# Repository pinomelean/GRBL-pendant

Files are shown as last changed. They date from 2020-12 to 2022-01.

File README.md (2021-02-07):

# GRBL-pendant

Hardware pendant intended for use with G-code senders for GRBL machines

### Description
The aim of this project is to produce a physical controller which functions similarly to a machine pendant, but is not limited to only that. The device would allow the user to interact with both the computer and the CNC machine without needing to reach for the mouse and keyboard for the most machining tasks.
The hardware is not limited to a single purpose, though, as the firmware can be easily changed so the controller can suit the needs of the user, and be adapted for their particular workflow.

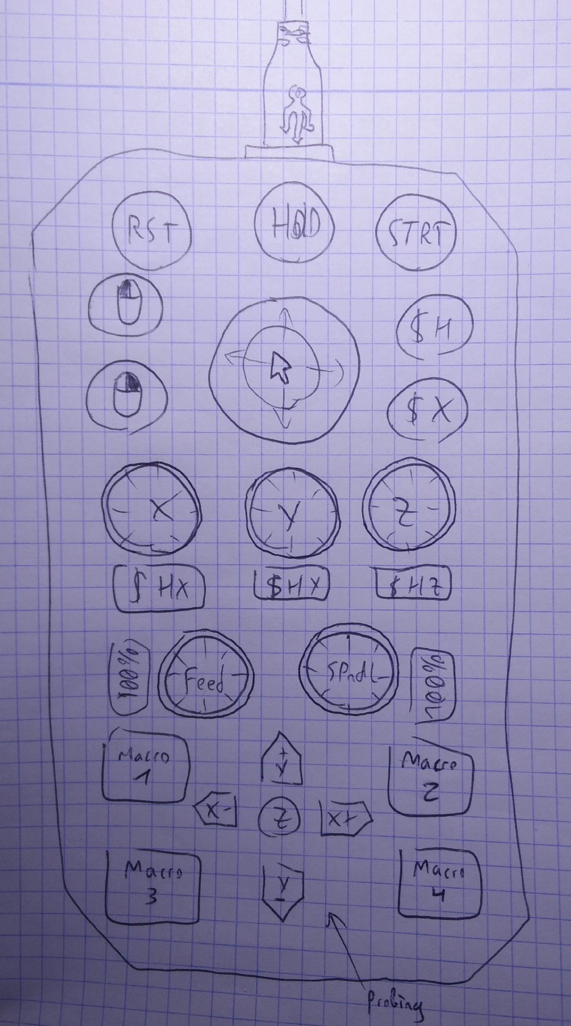
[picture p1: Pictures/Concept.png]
Initial concept drawing
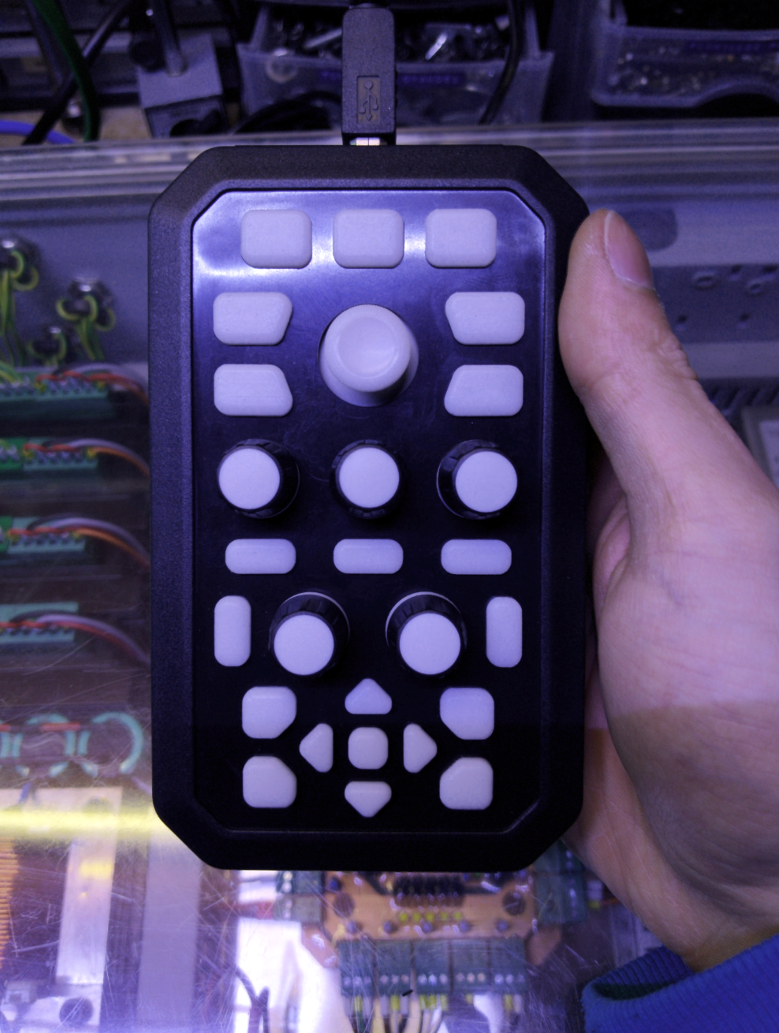
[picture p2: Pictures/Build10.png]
 	  

This USB pendant Includes many buttons, encoders and a thumbstick that can be configured with the most common functions and G-code commands you need to use your machine.
It uses a Teensy++ 2 because of its physical size, IO, native USB, and ease of programming with the Arduino ecosystem, *as limited as it is*.

### Free and open source

I publish all the files necessary for anyone to "DIY" it, all files can be opened and edited with FOSS software.
Anyone with a CNC mill/router should be able to make their own if they're so inclined.

The code is written as simple as I can manage (even if I suck at it), so anyone with basic knowledge and/or an Arduino tutorial open in another tab can modify it to suit their needs.

The PCBs are designed in KiCad and made to be simple enough to be milled at home, as I've done with the first prototype.

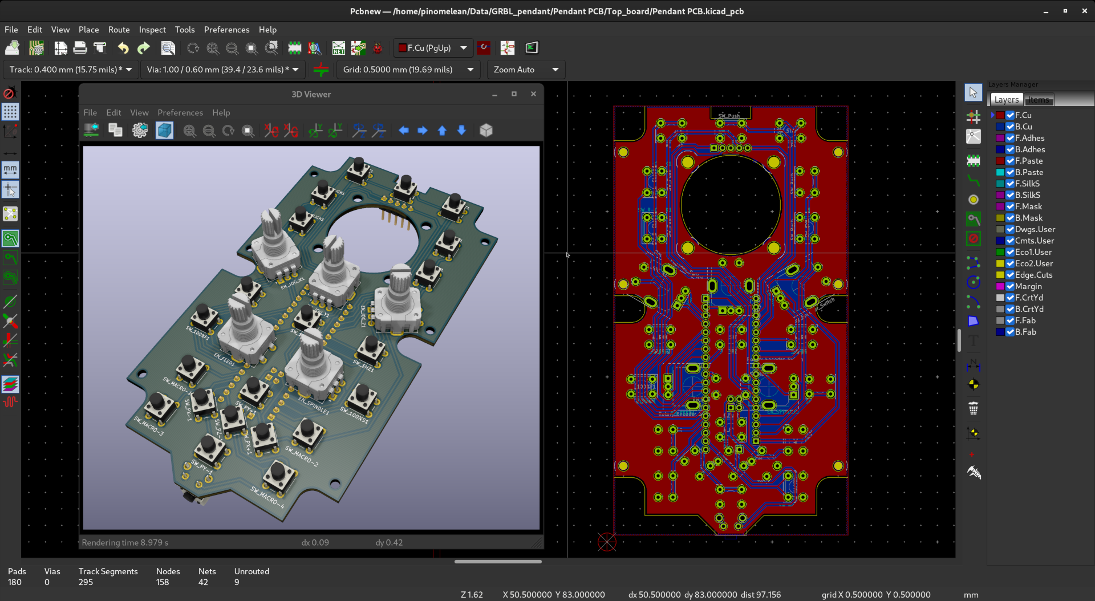
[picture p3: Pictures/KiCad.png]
KiCad


To mill the PCBs I used, and would recommend, [Juan Pablo Caram](https://github.com/jpcaram)'s [FlatCAM](http://www.flatcam.org/) and [Martin Pittermann](https://github.com/martin2250)'s [OpenCNCPilot](https://github.com/martin2250/OpenCNCPilot)

FreeCAD was used to design the silicone keypad and the mould to cast it.
The mould and the case were milled using toolpaths generated in the path workbench.

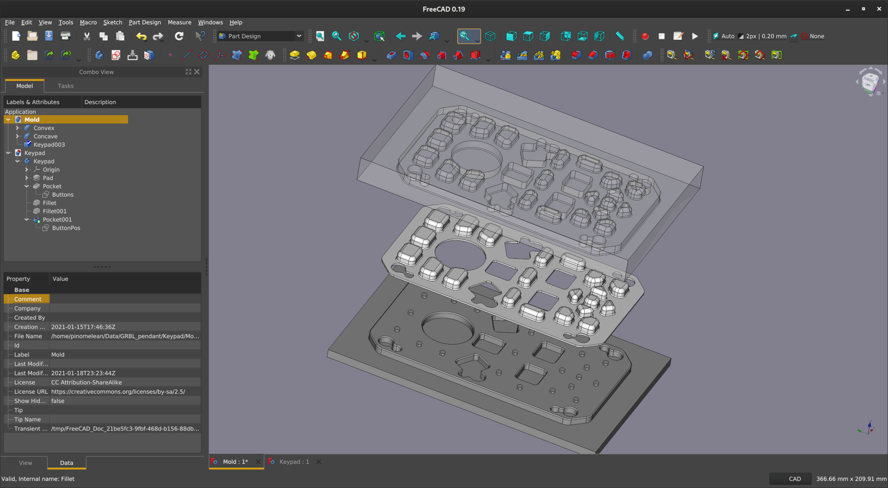
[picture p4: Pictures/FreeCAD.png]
FreeCAD


## Pendant layout

The layout I had in mind designing this pendant, and will come by default will be the following:

The Thumbstick is used either as a mouse pointer, along with a couple of buttons for clicking, or to quickly jog the machine when pressed in.

*The Teensy can emulate a game controller thumbstick, but as not many G-code sender applications support game controllers, and those that do (I only tested UGS) may not recognize the one emulated by the teensy, the thumbstick will not be emulating a game controller for nw, and just write G-code jog commands instead. This should work with any sender.*

The buttons at the top of the pendant are dedicated to the basic machine commands: Reset, Feed hold, Cycle start/Resume at the top, and Home machine and Kill alarm lock right of the thumbstick.

There are three encoders for fine jogging of each axis. By default each detent should result in 1mm of travel, and 0.1mm if the encoder is pushed in while turning.
Pushing an encoder without turning it will zero that axis.

The two other encoders are meant for Feed and spindle speed overrides, but could be used for jogging two extra axises in a 5-axis machine if anyone's running one of those.

*I still need to figure how to send the Feed and Spindle speed override command characters through a sender application if it does not have hotkeys for that*

Next to each encoder is a button which is used to individually home that axis.
For the Feed and Spindle encoders, the button resets it to 100%.

At the bottom of the controller are the macro buttons.
The five ones in the middle are used for probing or touching against a workpiece from every direction (except from under it).

The other 4 buttons are left for any extra macros the user could need, such as turning on/off mist/flood coolant, starting/stopping the spindle, touching a bit on the tool setter...

**Of course, all of the actions are remappable and configurable to suit the needs and workflow of the user. The defaults are just what** ***I*** **think is most useful**

## Project status

- Second version built. Looks much nicer in black and white. Probably final version if no issues arise.
	- The keypad also feels nice and works very well, but the Shore A20 durometer silicone might be too soft for this application, but will do for mow.



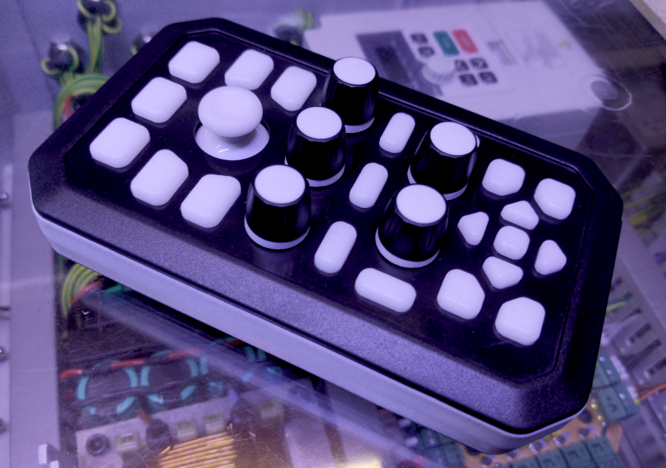
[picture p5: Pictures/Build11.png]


- Keypad mould machined. Couldn't get the 3D surfacing operation to work with a ball end mill en FreeCAD, so I had to resort to Fusion360 for that operation.
	- A sprue and vent have to be drilled manually into the side to inject the silicone with a syringe and push out the air.

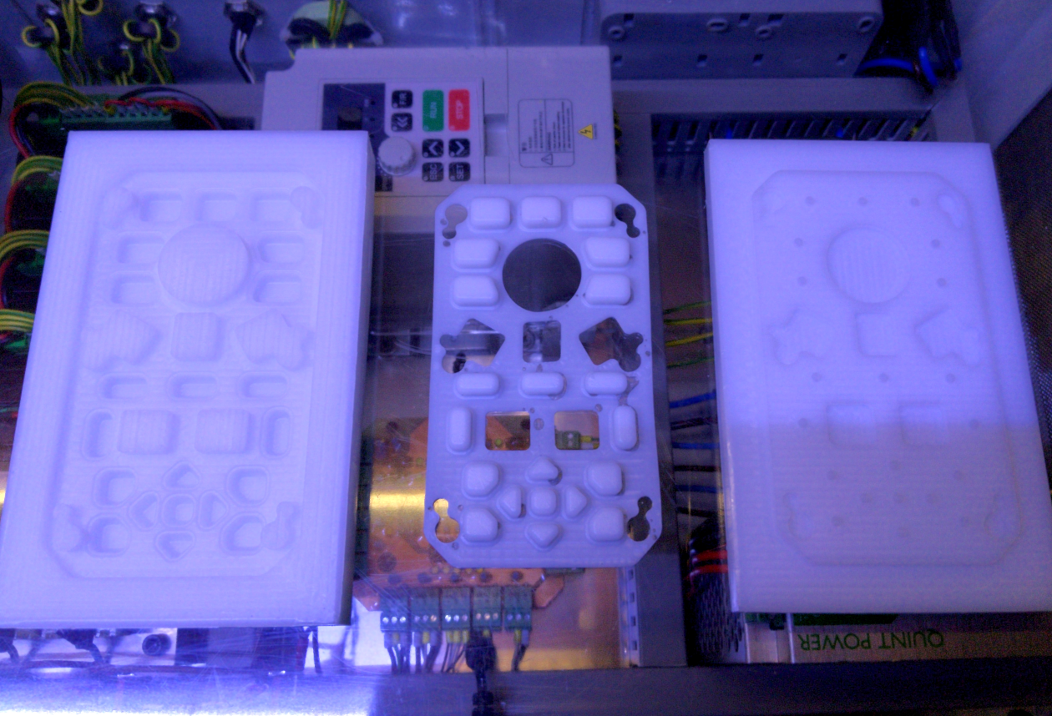
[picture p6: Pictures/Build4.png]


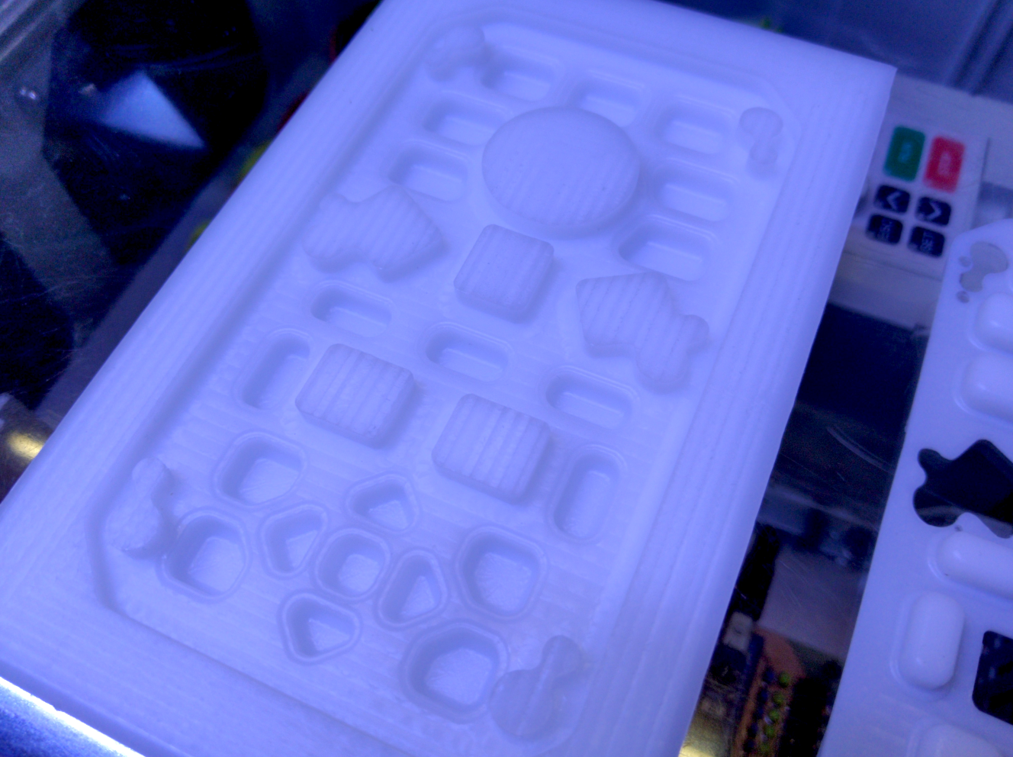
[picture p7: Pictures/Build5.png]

	
- First prototype mostly built, silicone keypad left to see how it all looks and feels. A couple of encoder push buttons don't work, but will do for testing.
	- Several adjustments made for a second version. Will not make a mold and keypad for the first.



- Thumbstick as mouse pointer - Done. Works pretty well in the smaller screens I use, slower in bigger ones, but it's adjustable.
- Thumbstick for jogging - UGS wouldn't recognize it in game controller mode, so It just types jogging G-code commands. Works ok.
- Encoder jogging - Works well for accurate positioning. Too slow for jogging around a bigger machine, but there's the thumbstick for that.
- Rest of the buttons - not yet programmed.

## Notes

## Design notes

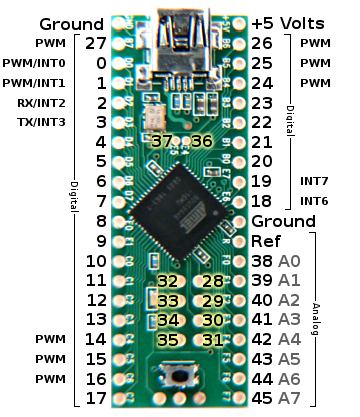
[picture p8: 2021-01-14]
Pictures/Teensy++2_pinout.png

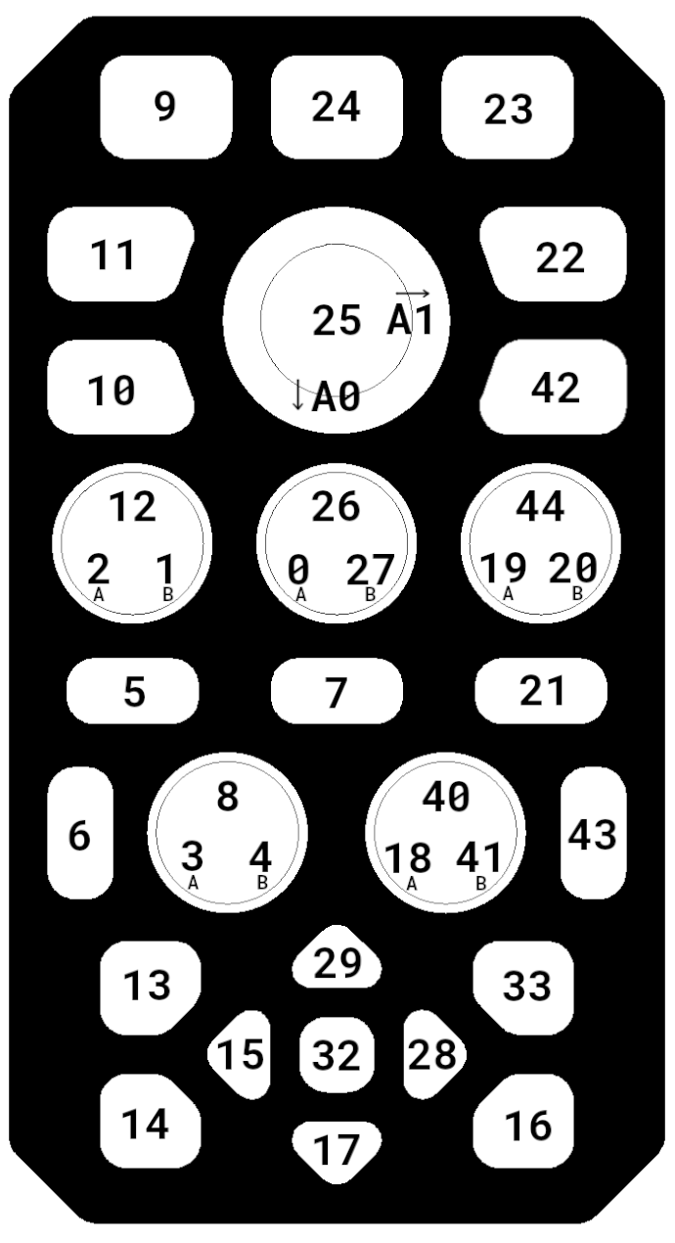
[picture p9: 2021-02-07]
Pictures/Pinout.png

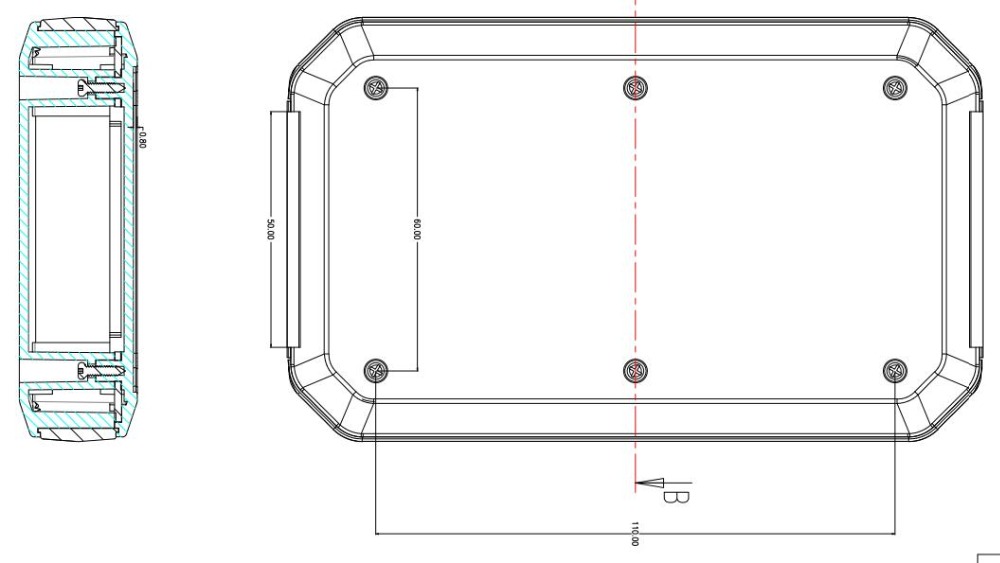
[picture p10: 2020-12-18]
Pictures/Case3.jpg

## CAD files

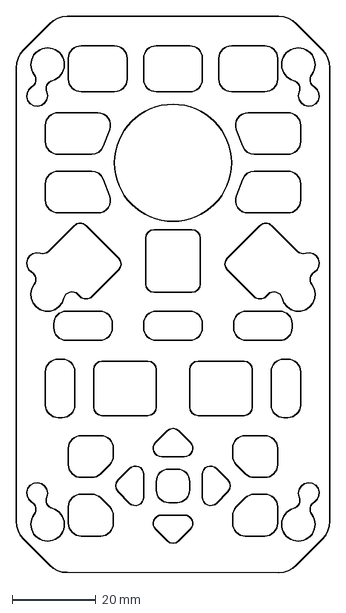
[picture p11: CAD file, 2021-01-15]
Case/Keypad/Keypad.dxf
75.0 x 133.0 mm

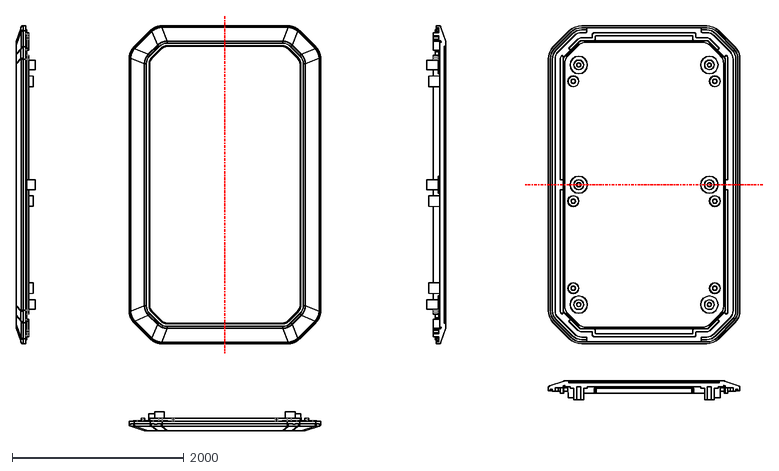
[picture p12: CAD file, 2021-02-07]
Case/Lid.dxf
8709.7 x 4838.7

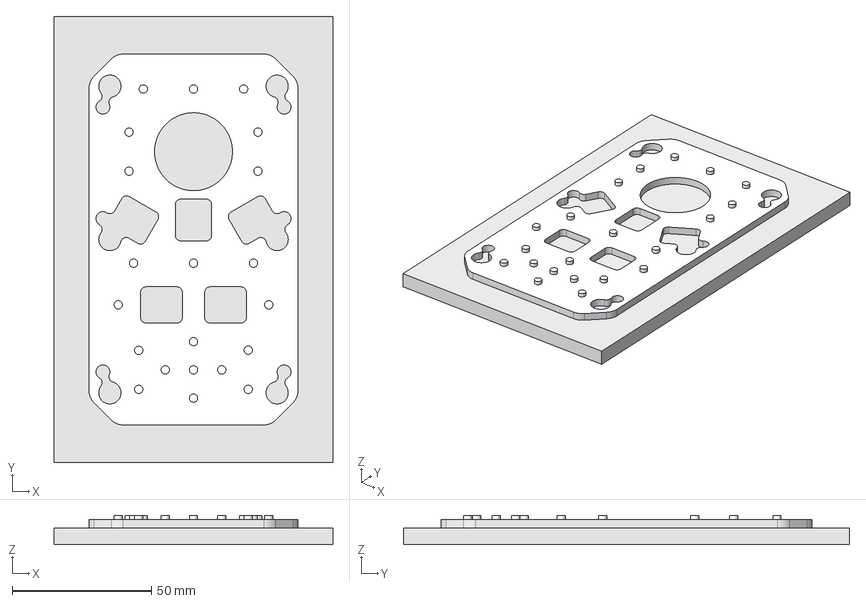
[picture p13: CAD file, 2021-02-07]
Keypad/Mold_Male.step
100.0 x 160.0 x 10.5 mm

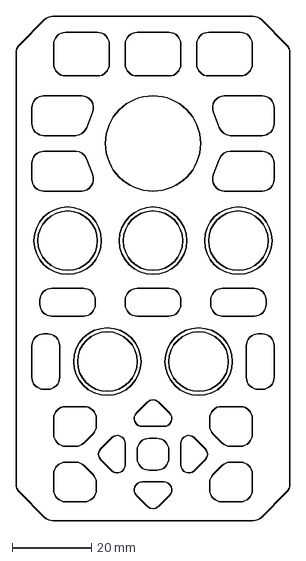
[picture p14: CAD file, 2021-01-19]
Layout.dxf
69.0 x 127.0 mm

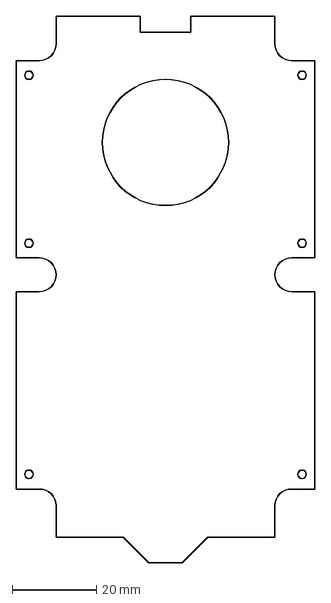
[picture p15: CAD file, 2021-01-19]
Pendant PCB/PCB outline.dxf
71.0 x 130.0 mm

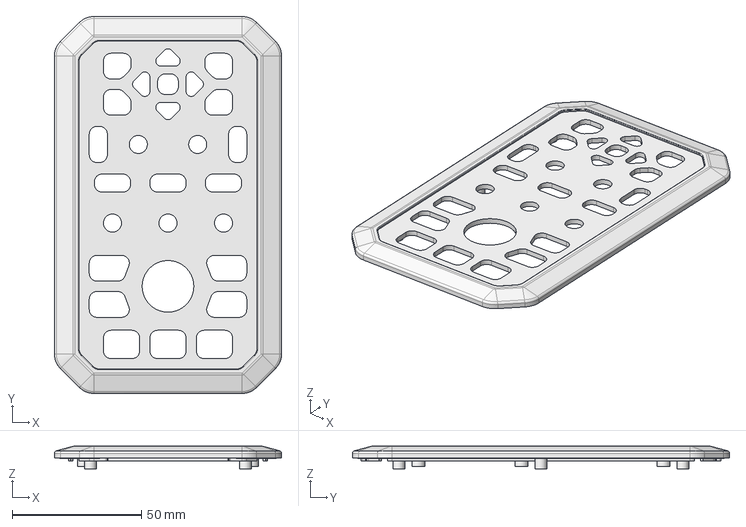
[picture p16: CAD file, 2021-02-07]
Case/Case_Lid.step
88.0 x 146.0 x 8.80 mm

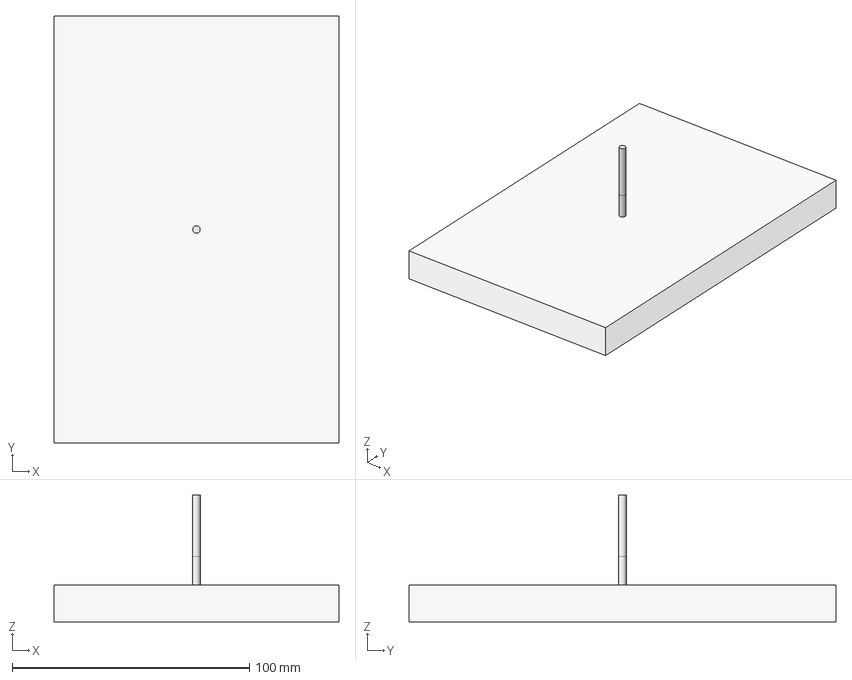
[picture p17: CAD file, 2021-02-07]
Keypad/Mold.FCStd
120.0 x 180.0 x 53.5 mm
Model-Cut003
Model-Cut
Stock
Stock001
2*4mm_Single_Flute
3.175*12mm_Single_Flute
3.175*12mm_Single_Flute002
2*4mm_Single_Flute002

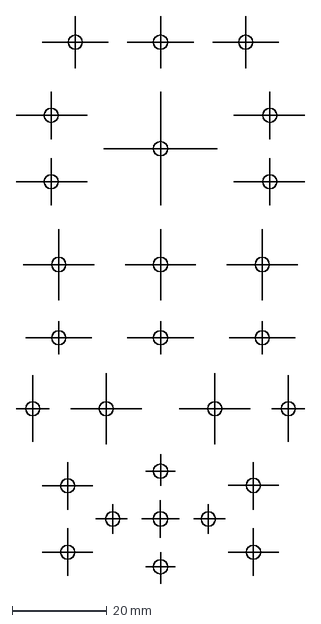
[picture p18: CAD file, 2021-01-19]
Pendant PCB/PCB positions.dxf
61.0 x 120.0 mm

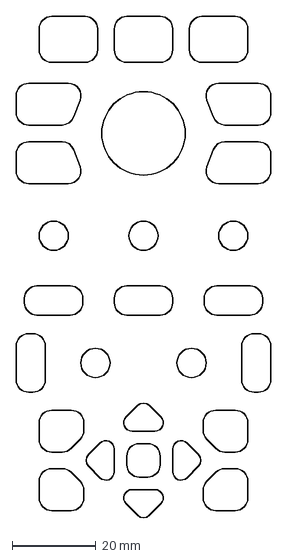
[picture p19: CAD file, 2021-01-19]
Case/Cutouts.dxf
61.0 x 120.2 mm

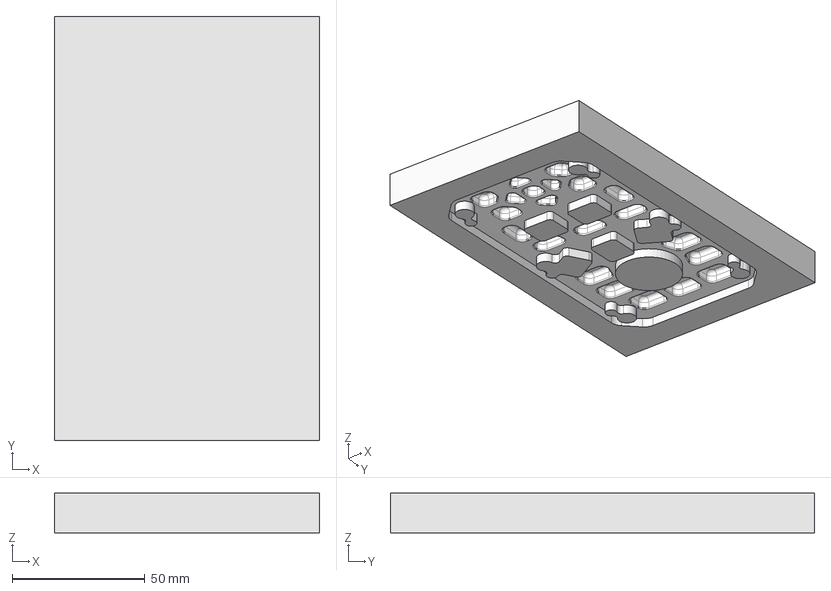
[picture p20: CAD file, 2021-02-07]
Keypad/Mold_Female.step
100.0 x 160.0 x 15.0 mm

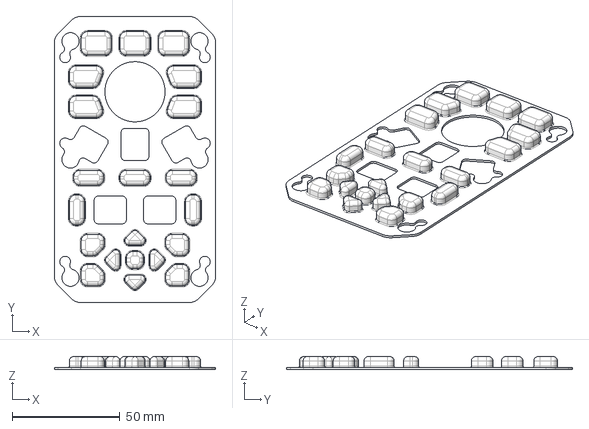
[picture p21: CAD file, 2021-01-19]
Keypad/Keypad.step
75.0 x 133.0 x 6.00 mm

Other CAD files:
Keypad/Keypad.FCStd
Keypad/Keypad.dxf

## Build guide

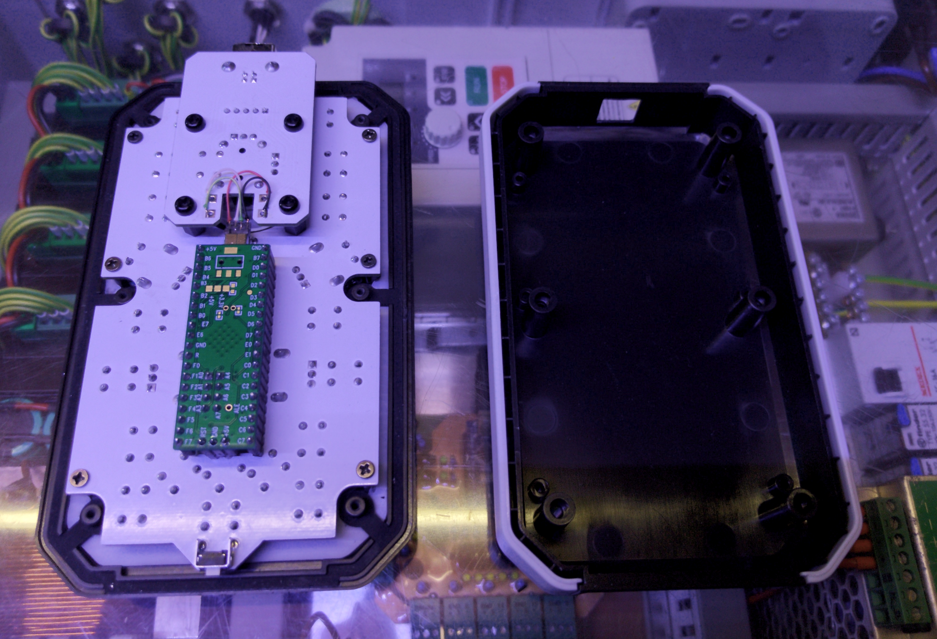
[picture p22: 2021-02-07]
Pictures/Build9.png

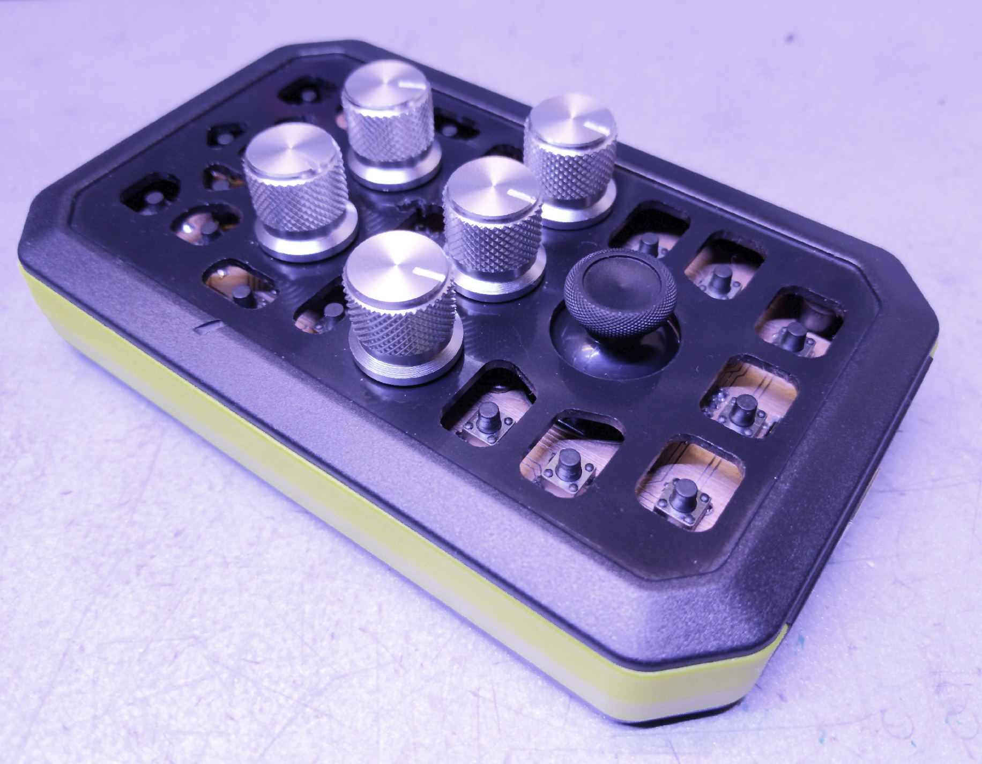
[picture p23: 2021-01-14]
Pictures/Build2.png

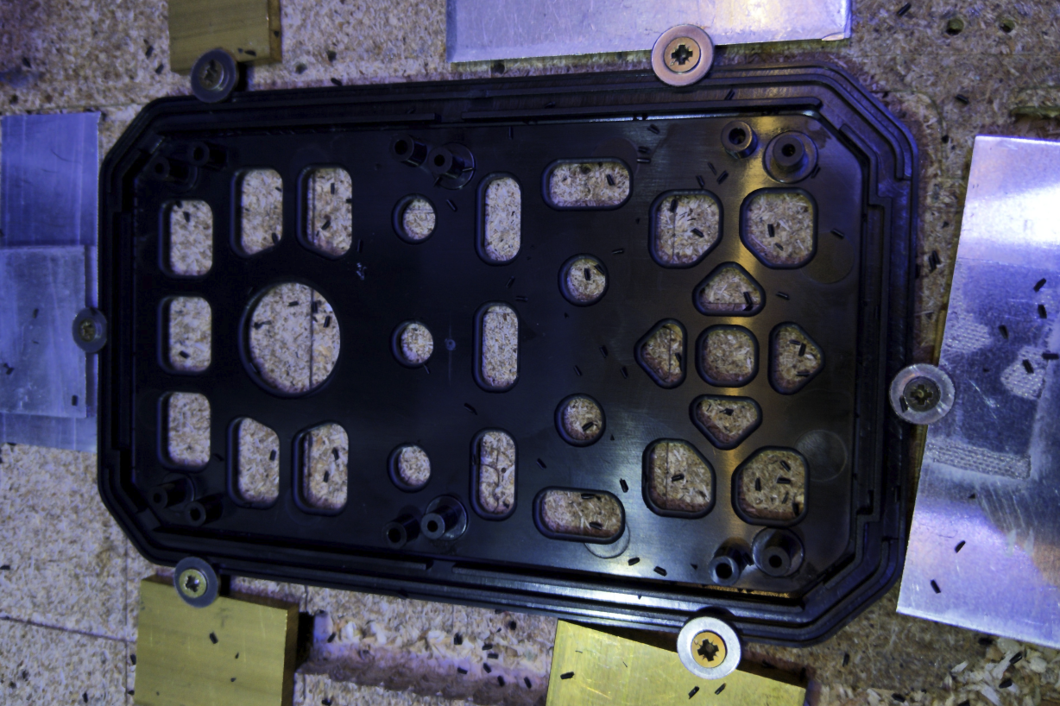
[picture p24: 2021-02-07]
Pictures/Build6.png

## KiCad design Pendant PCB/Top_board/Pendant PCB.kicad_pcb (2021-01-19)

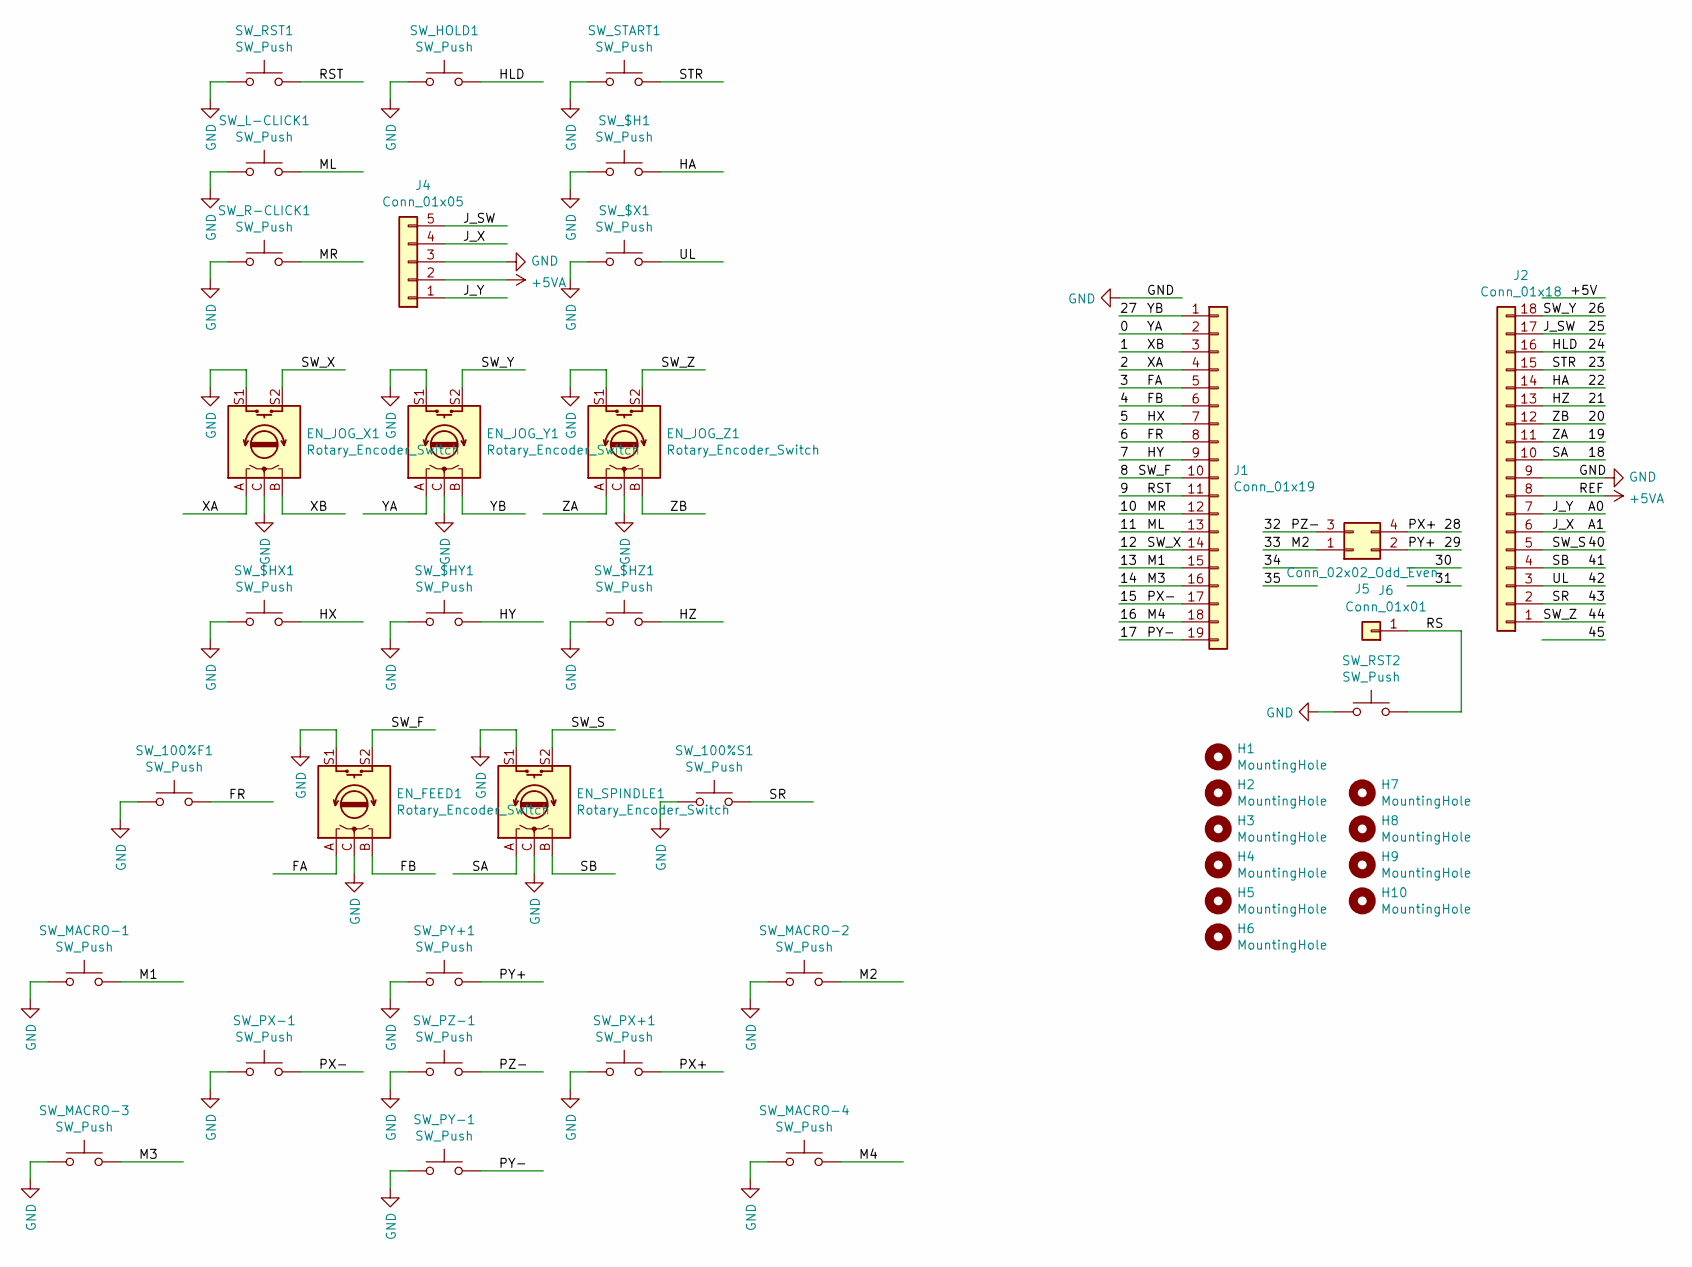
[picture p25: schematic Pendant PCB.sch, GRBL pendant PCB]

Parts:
EN_FEED1: Rotary_Encoder_Switch; PEC11R-4x15K
EN_JOG_X1: Rotary_Encoder_Switch; PEC11R-4x15K
EN_JOG_Y1: Rotary_Encoder_Switch; PEC11R-4x15K
EN_JOG_Z1: Rotary_Encoder_Switch; PEC11R-4x15K
EN_SPINDLE1: Rotary_Encoder_Switch; PEC11R-4x15K
H1, H2, H3, H4, H5, H6: MountingHole; MountingHole_2.5mm
H7, H8, H9, H10: MountingHole; MountingHole_3.2mm_M3
J1: Conn_01x19; PinHeader_1x19_P2.54mm_Vertical
J2: Conn_01x18; PinHeader_1x18_P2.54mm_Vertical
J4: Conn_01x05; PinHeader_1x05_P2.54mm_Vertical
J5: Conn_02x02_Odd_Even; PinHeader_2x02_P2.54mm_Vertical
J6: Conn_01x01; PinHeader_1x01_P2.54mm_Vertical
SW_100%F1, SW_100%S1: SW_Push; SW_PUSH_6mm_H7.3mm
SW_$H1: SW_Push; SW_PUSH_6mm_H7.3mm
SW_$HX1: SW_Push; SW_PUSH_6mm_H7.3mm
SW_$HY1: SW_Push; SW_PUSH_6mm_H7.3mm
SW_$HZ1: SW_Push; SW_PUSH_6mm_H7.3mm
SW_$X1: SW_Push; SW_PUSH_6mm_H7.3mm
SW_HOLD1: SW_Push; SW_PUSH_6mm_H7.3mm
SW_L-CLICK1: SW_Push; SW_PUSH_6mm_H7.3mm
SW_MACRO-1, SW_MACRO-2, SW_MACRO-3, SW_MACRO-4: SW_Push; SW_PUSH_6mm_H7.3mm
SW_PX+1: SW_Push; SW_PUSH_6mm_H7.3mm
SW_PX-1: SW_Push; SW_PUSH_6mm_H7.3mm
SW_PY+1: SW_Push; SW_PUSH_6mm_H7.3mm
SW_PY-1: SW_Push; SW_PUSH_6mm_H7.3mm
SW_PZ-1: SW_Push; SW_PUSH_6mm_H7.3mm
SW_R-CLICK1: SW_Push; SW_PUSH_6mm_H7.3mm
SW_RST1: SW_Push; SW_PUSH_6mm_H7.3mm
SW_RST2: SW_Push; SW_Tactile_SPST_Angled_PTS645Vx39-2LFS
SW_START1: SW_Push; SW_PUSH_6mm_H7.3mm

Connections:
+5VA: J2.8, J4.2
/0: EN_JOG_Y1.A, J1.2
/1: EN_JOG_X1.B, J1.3
/2: EN_JOG_X1.A, J1.4
/3: EN_FEED1.A, J1.5
/4: EN_FEED1.B, J1.6
/5: J1.7, SW_$HX1.2
/6: J1.8, SW_100%F1.2
/7: J1.9, SW_$HY1.2
/8: EN_FEED1.S2, J1.10
/9: J1.11, SW_RST1.1
/10: J1.12, SW_R-CLICK1.1
/11: J1.13, SW_L-CLICK1.1
/12: EN_JOG_X1.S2, J1.14
/13: J1.15, SW_MACRO-1.2
/14: J1.16, SW_MACRO-3.2
/15: J1.17, SW_PX-1.1
/16: J1.18, SW_MACRO-4.1
/17: J1.19, SW_PY-1.1
/18: EN_SPINDLE1.A, J2.10
/19: EN_JOG_Z1.A, J2.11
/20: EN_JOG_Z1.B, J2.12
/21: J2.13, SW_$HZ1.2
/22: J2.14, SW_$H1.1
/23: J2.15, SW_START1.1
/24: J2.16, SW_HOLD1.2
/25: J2.17, J4.5
/26: EN_JOG_Y1.S2, J2.18
/27: EN_JOG_Y1.B, J1.1
/28: J5.4, SW_PX+1.1
/29: J5.2, SW_PY+1.2
/32: J5.3, SW_PZ-1.1
/33: J5.1, SW_MACRO-2.1
/40: EN_SPINDLE1.S2, J2.5
/41: EN_SPINDLE1.B, J2.4
/42: J2.3, SW_$X1.1
/43: J2.2, SW_100%S1.2
/44: EN_JOG_Z1.S2, J2.1
/A0: J2.7, J4.1
/A1: J2.6, J4.4
/RS: J6.1, SW_RST2.2
GND: EN_FEED1.C, EN_FEED1.S1, EN_JOG_X1.C, EN_JOG_X1.S1, EN_JOG_Y1.C, EN_JOG_Y1.S1, EN_JOG_Z1.C, EN_JOG_Z1.S1, EN_SPINDLE1.C, EN_SPINDLE1.S1, J2.9, J4.3, SW_100%F1.1, SW_100%S1.1, SW_$H1.2, SW_$HX1.1, SW_$HY1.1, SW_$HZ1.1, SW_$X1.2, SW_HOLD1.1, SW_L-CLICK1.2, SW_MACRO-1.1, SW_MACRO-2.2, SW_MACRO-3.1, SW_MACRO-4.2, SW_PX+1.2, SW_PX-1.2, SW_PY+1.1, SW_PY-1.2, SW_PZ-1.2, SW_R-CLICK1.2, SW_RST1.2, SW_RST2.1, SW_START1.2

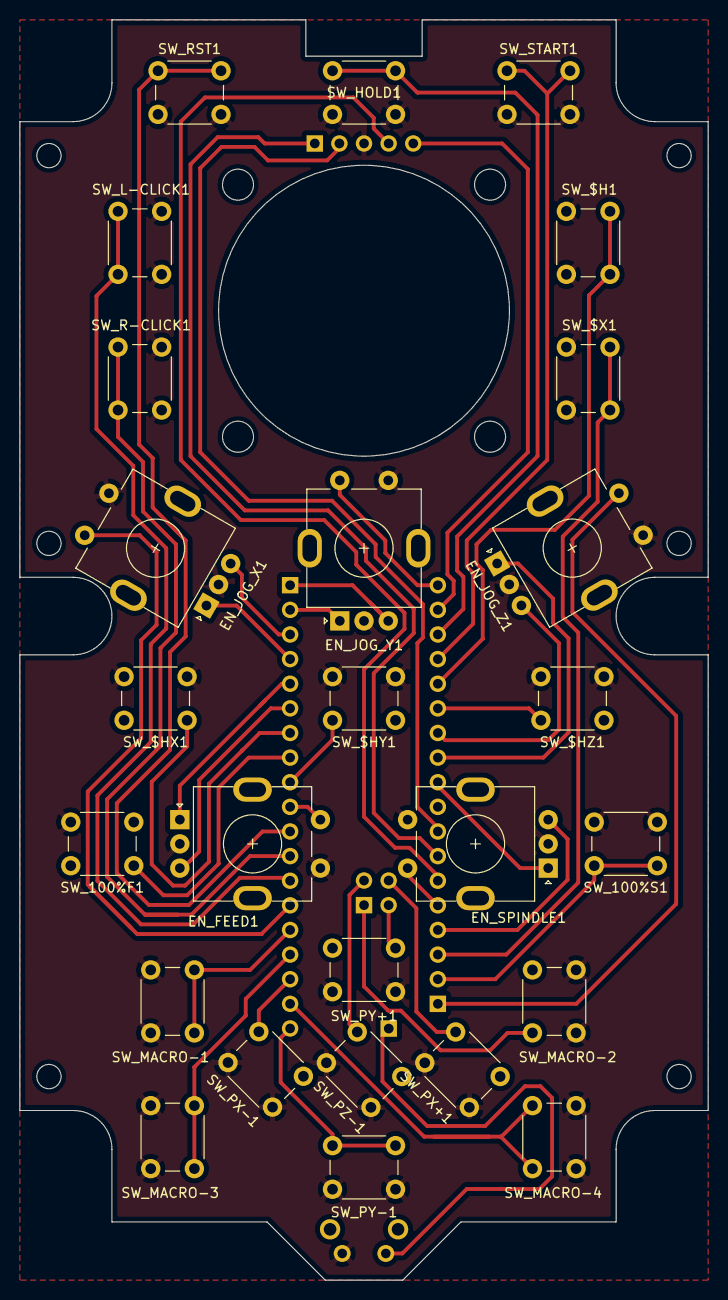
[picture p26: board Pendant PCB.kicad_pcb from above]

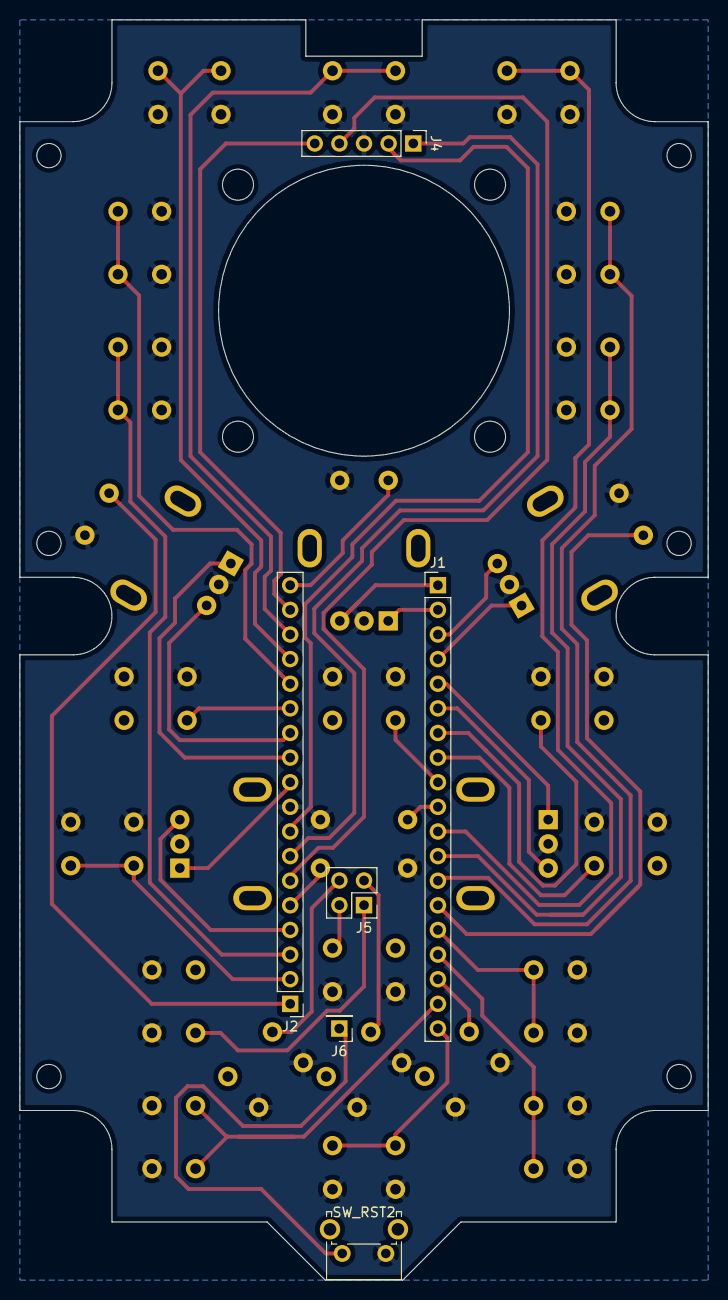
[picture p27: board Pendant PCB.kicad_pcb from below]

Board: 2 copper layers, 71.0 x 130.0 mm, 42 parts (6 on the bottom side), 42 nets.

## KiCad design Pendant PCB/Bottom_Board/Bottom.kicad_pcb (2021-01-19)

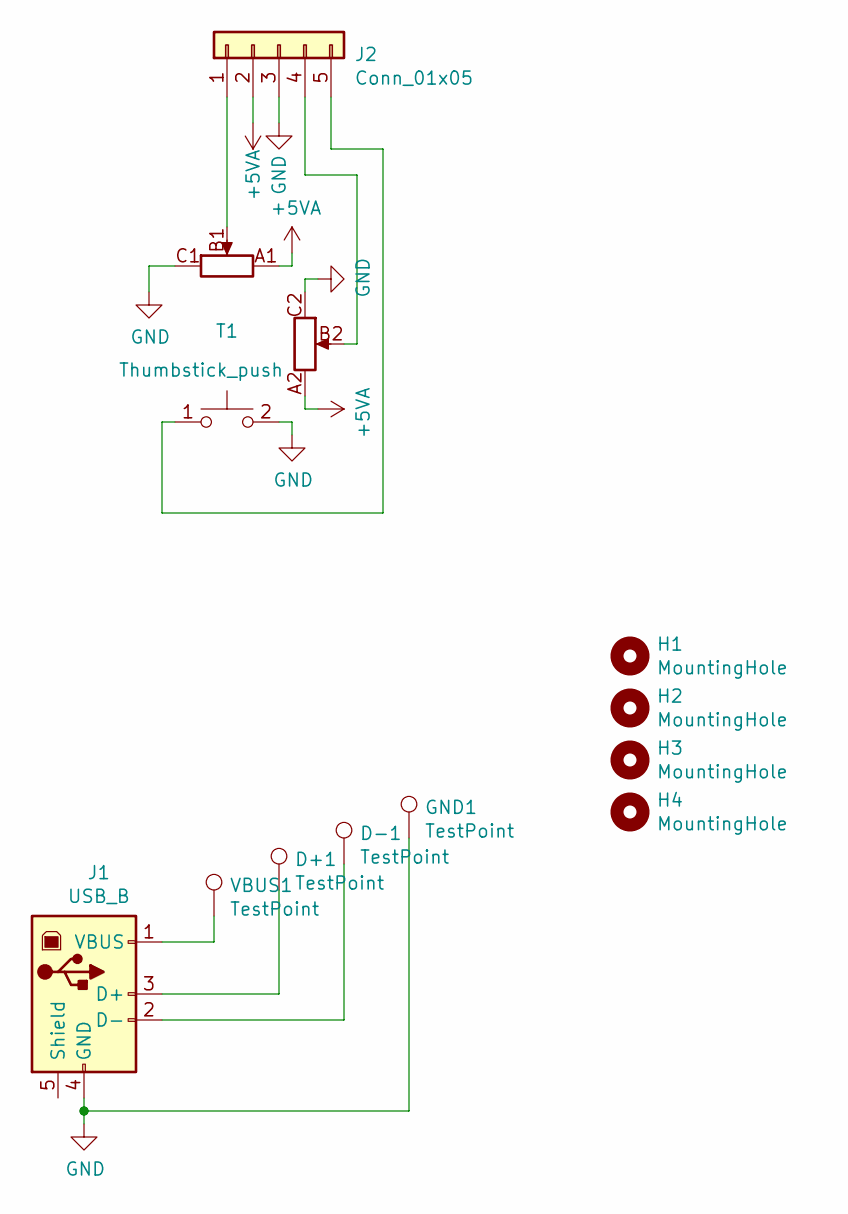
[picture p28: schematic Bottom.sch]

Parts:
D+1: TestPoint; TestPoint_THTPad_2.5x2.5mm_Drill1.2mm
D-1: TestPoint; TestPoint_THTPad_2.5x2.5mm_Drill1.2mm
GND1: TestPoint; TestPoint_THTPad_2.5x2.5mm_Drill1.2mm
H1, H2, H3, H4: MountingHole; MountingHole_3.2mm_M3
J1: USB_B; USB_B_Horizontal
J2: Conn_01x05; PinSocket_1x05_P2.54mm_Vertical
T1: Thumbstick_push; RKJXV1224_CAP
VBUS1: TestPoint; TestPoint_THTPad_2.5x2.5mm_Drill1.2mm

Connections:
+5VA: J2.2, T1.A1, T1.A2
GND: GND1.1, J1.4 (GND), J2.3, T1.2, T1.C1, T1.C2
unnamed: D+1.1, J1.3 (D+)
unnamed: D-1.1, J1.2 (D-)
unnamed: J1.1 (VBUS), VBUS1.1
unnamed: J2.1, T1.B1
unnamed: J2.4, T1.B2
unnamed: J2.5, T1.1

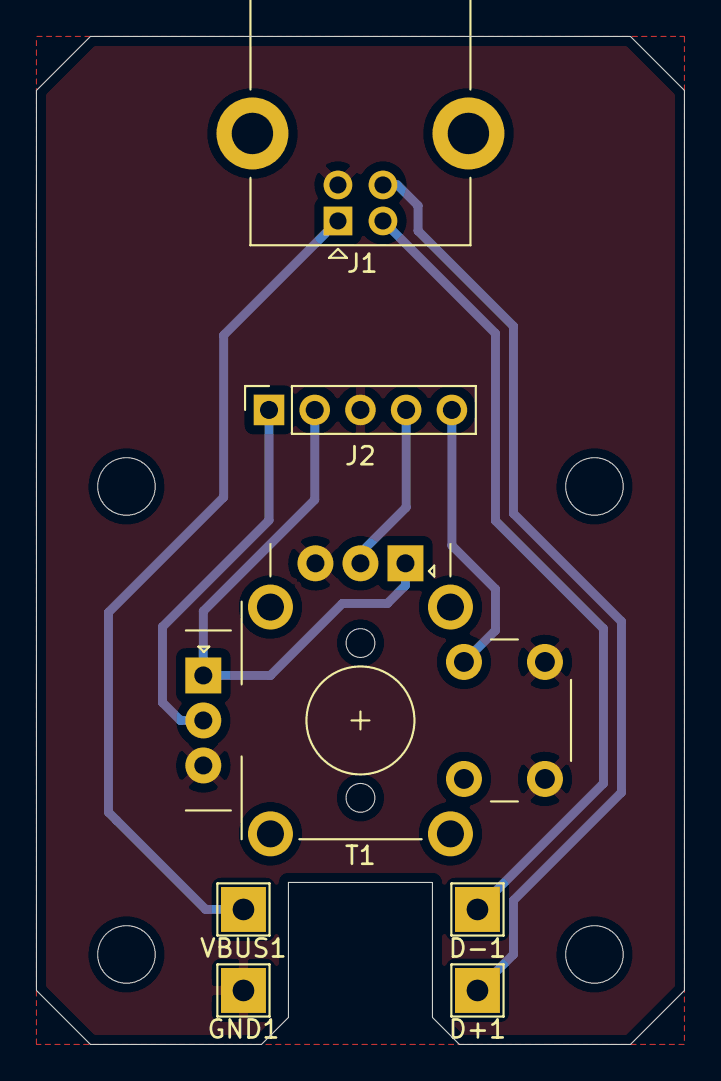
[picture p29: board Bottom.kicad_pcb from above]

Board: 2 copper layers, 36.0 x 56.0 mm, 11 parts (0 on the bottom side), 8 nets.

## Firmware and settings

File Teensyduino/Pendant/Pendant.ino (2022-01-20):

/*  PENDANT LAYOUT WITH PIN CONNECTIONS
      ________________________________
    /   ______     ______     ______   \
   /   |      |   |      |   |      |   \
  /    |   9  |   |  24  |   |  23  |    \
 |     |______|   |______|   |______|     |
 |   ________                  ________   |
 |  |        |    ________    |        |  |
 |  |  11   /   /          \   \   22  |  |
 |  |_____ /   |         >  |   \ _____|  |
 |   _____     |     25  A1 |     _____   |
 |  |      \   |   v A0     |   /      |  |
 |  |  10   \   \ ________ /   /   42  |  |
 |  |________|                |________|  |
 |      ____        ____        ____      |
 |    /  12  \    /  26  \    /  44  \    |
 |   (  2  1  )  (  0 27  )  ( 19  20 )   |
 |    \ ____ /    \_____ /    \ ____ /    |
 |     ______      ______      ______     |
 |    |  5   |    |  7   |    |  21  |    |
 |    |______|    |______|    |______|    |
 |   ___      ____        ____      ___   |
 |  |   |   /  8   \    /  40  \   |   |  |
 |  | 6 |  (  3  4  )  ( 18  41 )  | 41|  |
 |  |___|   \ ____ /    \ ____ /   |___|  |
 |     ______        __        ______     |
 |    |      |     / 29 \     |      |    |
 |    | 13  /     ( ____ )     \  33 |    |
 |    |___ /   __   ____   __   \ ___|    |
 |           /   | |    | |   \           |
 |          ( 15 | | 32 | | 28 )          |
 |     ___   \ __| |____| |__ /   ___     |
 |    |    \        ____        /    |    |
  \   | 14  \     (  17  )     /  16 |   /
   \  |______|     \ __ /     |______|  /
    \ ________________________________ /

 25 - thumbstick push button
 A1, and A0 - thumbstick axes
 12, 26, 44, 8, and 40 - encoder push buttons
 2, 1; 0, 27; 19, 20; 3, 4; and 18, 41; - encoder quadrature outputs
*/
 
#include <Keyboard.h>
#include <Encoder.h>
#include <Mouse.h>
#include <math.h>
#include <Button.h> //Change the debouncing delay to 100ms or fewer


//Thumbstick
Button stickButton=25; //Thumbstick inputs
const int xAxis=A1;
const int yAxis=A0;
Button clickL=11; //Mouse buttons
Button clickR=10;
int xoff,yoff; //Startup position offset

void mouse();

//Jogging encoders
int encoder_jog(Encoder &,Button Push,float &,char Axis,unsigned int Feed); 
int Vjog=1500;  //Maximum jogging speed at 1mm/detent
Encoder xEnc(2,1); 
Button xButton=12;
Encoder yEnc(0,27); 
Button yButton=26;
Encoder zEnc(19,20); 
Button zButton=44;
bool enc[3]={0,0,0}; //Flag vector to chech for encoder rotation
 

void setup() {
  //Thumbstick setup
  stickButton.begin();
  clickL.begin();
  clickR.begin();
  //Set starting position as 0,0
  xoff=analogRead(xAxis);
  yoff=analogRead(yAxis);
  
  Mouse.begin();
  //Encoder setup
  xButton.begin();
  yButton.begin();
  zButton.begin();
} 
 
void loop() { 
  delay(10-(millis()%10)); //10ms min loop time

  //Thumbstick mouse
  if(stickButton.read()==Button::RELEASED)mouse();
  
  //Jogging encoders 
  if((millis()%100<=10)){ //executes every 100ms
    enc[0]+=encoder_jog(xEnc,xButton,'X',Vjog);
    if(xButton.pressed())enc[0]=0; //Pulses are counted starting when pushed in
    //If he encoder is pushed and released without turning, the axis is zeroed
    if(xButton.released()&&enc[0]==0)Keyboard.println("G10 L20 P0 X0"); 
    enc[1]+=encoder_jog(yEnc,yButton,'Y',Vjog);
    if(yButton.pressed())enc[1]=0;
    if(yButton.released()&&enc[1]==0)Keyboard.println("G10 L20 P0 Y0");
    enc[2]+=encoder_jog(zEnc,zButton,'Z',Vjog);
    if(zButton.pressed())enc[2]=0;
    if(zButton.released()&&enc[2]==0)Keyboard.println("G10 L20 P0 Z0");
  }
  
} 

void mouse(){
  //Pointer movement
  int range=10; //Maximum movement speed. Default:10
  int dead=25; //Dead zone. Increase to mask drift.
  int x=analogRead(xAxis)-xoff;
  int y=-(analogRead(yAxis)-yoff);
  signed char mx=0,my=0;
  if(abs(x)>dead){
    mx=map(abs(x),dead,512,1,range);
    if(x<0)mx=-mx;
  }
  if(abs(y)>dead){
    my=map(abs(y),dead,512,1,range);
    if(y<0)my=-my;
  }
  if(mx!=0||my!=0)Mouse.move(mx,my,0);
  
  //Mouse buttons control
   if(clickL.pressed())Mouse.press(MOUSE_LEFT);
   if(clickL.released())Mouse.release(MOUSE_LEFT);
   
   if(clickR.pressed())Mouse.press(MOUSE_RIGHT);
   if(clickR.released())Mouse.release(MOUSE_RIGHT);
}

int encoder_jog(Encoder &E,Button Push,char Axis,unsigned int Feed){ 
  float d=E.read(); 
  if(d>=4||d<=-4){  //Each detent generates 4 pulses
    d=(int)d/4; //Pulses reduced to only 1 per detent
    Keyboard.print("$J=G91 "); 
    Keyboard.print(Axis); 
    if(d<0)Keyboard.print("-"); 
    d=abs(d); 
    //If the encoder is pushed in, both the distance and speed are reduced to 1/10 for precise positioning
    Keyboard.print(((Push.read()==Button::PRESSED)?d/10:d)); 
    Keyboard.print(" F"); 
    Keyboard.println(((Push.read()==Button::PRESSED)?Feed/10:Feed)); 
    E.write(0); 
    return 1; 
  } 
  else{ 
    return 0; 
  } 
} 

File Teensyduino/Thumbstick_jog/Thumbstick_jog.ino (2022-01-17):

#include "Keyboard.h"

//Thumbstick inputs
const int stickButton=25;
const int xAxis=A1;
const int yAxis=A0;
int xoff,yoff; //Startup position offset
bool jogging;

float jog(int f);

void setup() {
  //Set starting thumbstick position as 0,0
  xoff=analogRead(xAxis);
  yoff=analogRead(yAxis);
  jogging=false;
  pinMode(stickButton, INPUT_PULLUP);
  
  Keyboard.begin();
}

void loop() {
  delay(10-(millis()%10)); //10ms min loop time
  if((millis()%100<=10))jog(2000);
}

float jog(int f){
  int dead=5; //Stick dead zone
  int stepFactor=15; //Set according to machine (default 15)
  //smaller factor => choppier movement
  //bigger factor => response delay (stopping)
  float x=analogRead(xAxis)-xoff;
  float y=analogRead(yAxis)-yoff;
  float d=sqrt(sq(x)+sq(y));
  if((d>=dead)&&(digitalRead(stickButton)==LOW)){
    jogging=true;
    float jx=(abs(x)>dead)?x/(f/stepFactor):0;
    float jy=(abs(y)>dead)?y/(f/stepFactor):0;
    Keyboard.print("$J=G91 X");
    Keyboard.print(jx);
    Keyboard.print(" Y");
    Keyboard.print(jy);
    Keyboard.print(" F");
    Keyboard.println(map(d/20,0,512/20,100,f));
    return d;
  }
  else{
    if(jogging){
      Keyboard.println("G4P0");
    }
    jogging=false;
    return 0;
  }

  
}

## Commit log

2020-12-21 Added Teensy(duino) pinout for reference
2020-12-24 KiCAD project added. Layout and PCB drawings updated for cheap case
    [Layout.dxf, PCB outline.dxf, Pendant PCB.kicad_pcb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]
2020-12-25 Drawings updated
    [keyboard.dxf]
2020-12-26 PCB prepared. Drawings updated
    [Layout.dxf, PCB outline.dxf, PCB positions.dxf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]
2021-01-04 PCB routed. Feed and Spindle encoders moved .5mm closer to Y-axis
    [Pendant PCB.kicad_pcb, Pendant PCB.sch]
2021-01-06 Bottom board (Thumbstick + USB)
    [Bottom.kicad_pcb, Bottom.sch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]
2021-01-07 Boards finished and revised. Fabrication outputs generated.
    [Bottom.kicad_pcb, Bottom.sch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]
2021-01-09 updated cutout path
    [Cutout_2mm_mill.dxf, cutout.dxf]
2021-01-09 Cutout as gerber for CAM processing
    [Cutout_2mm_mill.dxf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]
2021-01-13 Encoder/thumbstick jog & mouse
2021-01-14 Readme improved.
    [Bottom-B_Cu.gbr, Bottom-B_Mask.gbr, Bottom-B_SilkS.gbr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]
2021-01-15 Keypad 3D model and mold
    [Keypad.FCStd, Keypad.dxf, Keypad.step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]
2021-01-19 Changes made for 2nd version.
    [Bottom-B_Cu.gbr, Bottom-B_Mask.gbr, Bottom-B_SilkS.gbr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]
2021-01-28 Started keypad mold machining
    [Mold.FCStd]
2021-02-07 Second version built, fabrication files included
    [Case_Lid.step, Lid.dxf, Mold.FCStd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]
2021-02-14 Encoder Jogging completed
